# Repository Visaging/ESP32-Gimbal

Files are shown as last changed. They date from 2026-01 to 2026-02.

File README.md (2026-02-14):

# Over-Engineered Stick (ESP32-S3 Gimbal)
Because apparently holding a phone parallel to the ground requires too much caloric burn for the modern human, I spent some time engineering a robot to do it for me. This is a custom 3-axis gimbal powered by an ESP32-S3, designed to compensate for your lack of wrist stability and general unwillingness to hold a steady shot.

## The "Why Did I Build This" Stack:
- **MCU:** ESP32-S3-WROOM-1-N8R2 _(Because a simple Arduino wasn't overkill enough)_
- **Sensors:** BMI270 6-Axis IMU _(To feel every single one of your hand tremors)_
- **Drivers:** 3x DRV8313 Three-Phase Drivers _(So the phone floats magically while you do nothing)_
- **Motors:** 2805 140KV Gimbal BLDC Motors _(To turn in exactly the opposite direction like she did)_
- **Power:** Custom 3S Li-Ion BMS with CN3303 Charging & TPS563200 Regulation _(Because USB 5V is for the weak)_

## Key Features
- **Active Stabilization:** Uses high-frequency FOC math to micro-manage gravity so you don't have to use "muscles".
- **Native USB-C:** One cable to code it and charge it, because looking for two different cables is just too much work.
- **3 Operation Modes:**
   * Stabilize: Standard horizon leveling and pan following.
   * Teaching Mode: Disables the motors so you can twist the camera to any weird angle by hand. After 5 seconds of holding it there, the gimbal accepts its new reality and locks that position.
   * Selfie/Statue Mode: A dedicated mode that gives you 6 seconds to pose the camera, then freezes it in place indefinitely because apparently holding a selfie angle is considered cardio now.
<hr></hr>
<details>
  <summary><h2>External Wiring Diagrams</h2></summary>
  
### Battery:

<!--
https://mermaid.live/edit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
-->
<hr></hr>

### Handle wiring:

<!--
https://mermaid.live/edit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
-->
<hr></hr>

### BMI270 Breakout Board:

<!--
https://mermaid.live/edit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
-->
<hr></hr>

### Motors:

<!--
https://mermaid.live/edit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
-->

</details>
<hr></hr>
<details>
  <summary><h2>PCB Schematics</h2></summary>


</details>
<hr></hr>
<details>
  <summary><h2>PCB Layout and Render</h2></summary>


</details>
<hr></hr>
<details>
  <summary><h2>Custom Body (3D Model)</h2></summary>

### Handle:


<hr></hr>

### Handle Top:


<hr></hr>

### Handle Enclosure:


<hr></hr>

### PAN Arm :


<hr></hr>

### ROLL Arm:


<hr></hr>

### PITCH Arm:


<hr></hr>

### PITCH Arm Cover:


<hr></hr>

### Tripod Enclosure:


<hr></hr>

### Tripod Hub:


<hr></hr>

### Tripod Legs:


</details>
<hr></hr>

## Financial Damage Report (Bill of Material)
BOM can be found in the  root older as a .csv, and is also viewable here: [Custom Gimble BOM](https://docs.google.com/spreadsheets/d/1aBBvSRlrgi5838ZnFZRnFuO4f2IFtYvHOy1n1r-4Mq0/edit?usp=sharing)
<details>
  <summary>Lion Circuits Order Order</summary>
  



</details>
<details>
  <summary>Carts</summary>
  
### Robu
  
Robu
<hr></hr>

### OnlyScrews

OnlyScrews
<hr></hr>

### ElectroPi

ElectroPi
<hr></hr>

### Evalta

Evalta
<hr></hr>

### DNA Tech India


<hr></hr>

### Amazon
Amazon
</details>

## Future Bugs... I Mean Features (Roadmap)
Things I might add if I ever get bored of it working perfectly

- [ ] Bluetooth App: Control the gimbal with a phone _(because looking at two screens is better than one)._
- [ ] Face Tracking: If I can figure out how to run AI on this chip without it catching fire.

## Liability Waiver (License)
**License:** MIT

Feel free to steal this code, modify it, or sell it. However, if your phone falls out and breaks because you set the PID values wrong, I legally never met you.

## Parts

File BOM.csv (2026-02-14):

Item | Description | Quantity | Unit Price ($) | Total Price ($) | URL | Total ($)
PCBA | PCB | 5 PCB, 1 PCBA | 167.9 | 167.9 | https://jlcpcb.com/ | 167.9
BMI270 Breadout Board | IMU | 1 | 3.46 | 3.46 | https://evelta.com/7semi-bmi270-nano-6-axis-imu-sensor-board-qwiic/ | 171.36
2805 140KV BLDC Motors | Motors | 3 | 11.88 | 35.64 | https://www.electropi.in/2805-140kv-gimbal-brushless-motor | 207
3.6v 2600mah 18650 Li-Ion Battery | Battery | 3 | 2.4 | 7.2 | https://robu.in/product/bak-nmc-18650-2600mah-3c-lithium-ion-3-6v-battery/ | 214.2
18650 3×1 Cell Spacer | Cell Spacer | 2 | 0.011 | 0.022 | https://robu.in/product/18650-3x1-battery-cell-spacer-holder/ | 214.222
3S 10A Li-ion 18650 BMS | BMS | 1 | 1.48 | 1.48 | https://robu.in/product/3s-6a-li-ion-18650-charger-protection-board-module-10-8v-11-1v-12-6v/ | 215.702
DS-316 10MM Momentary Push Button | Push Buttons | 3 | 0.25 | 0.75 | https://robu.in/product/red-ds-316-10mm-lock-free-momentary-self-reset-small-push-button-switch/ | 216.452
3A 250V Rocker Swtich | Power Botton | 1 | 0.27 | 0.27 | https://robu.in/product/1-month-warranty-1217/ | 216.722
3mm LED Orange | LED | 8 | 0.014 | 0.112 | https://robu.in/product/3mm-dip-led-orange-50-pcs/ | 216.834
30AWG Silicon Wire (Red) | Connecting Wire | 5 | 0.055 | 0.275 | https://robu.in/product/high-quality-ultra-flexible-30awg-silicone-wire-1000-m-red/ | 217.109
30AWG Silicon Wire (Black) | Connecting Wire | 5 | 0.055 | 0.275 | https://robu.in/product/high-quality-ultra-flexible-30awg-silicone-wire-1000-m-black/ | 217.384
30AWG Silicon Wire (Yellow) | Connecting Wire | 5 | 0.055 | 0.275 | https://robu.in/product/high-quality-ultra-flexible-30awg-silicone-wire-yellow/ | 217.659
30AWG Silicon Wire (Green) | Connecting Wire | 5 | 0.055 | 0.275 | https://robu.in/product/high-quality-ultra-flexible-30awg-silicone-wire-green/ | 217.934
CN3303 | Booster Chip | 1 | 0.55 | 0.55 | https://www.dnatechindia.com/cn3303-pfm-three-cell-lithium-battery-ic.html | 218.484
TYPE-C-31-M-12 | USB-C Port | 1 | 0.42 | 0.42 | https://robu.in/product/type-c-31-m-12-hroparts-5a-1-16p-female-type-c-smd-usb-connectors-rohs/?gad_source=1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 | 218.904
Universal Mobile Holder | Mobile Holder | 1 | 1.54 | 1.54 | https://www.amazon.in/gp/product/B07S9KNGVS | 220.444
M2 and M3 Screws | Mounting Screws | 1 | 4.41 | 4.41 | https://www.amazon.in/gp/product/B0FP53QGD2/ | 224.854
3M VHB Tape | Mounting PCB | 1 | 1.22 | 1.22 | https://onlyscrews.in/products/3m%E2%84%A2-foam-tape-12mm-x-5meters | 226.074
M3 x 10mm Screws | Mounting Screws | 4 | 0.015 | 0.06 | https://onlyscrews.in/products/phillips-csk-m3-x-8mm-pack-of-20? | 226.134
M3 x 8mm Inserts | Mounting Inserts | 4 | 0.029 | 0.116 | https://onlyscrews.in/products/m3-x-8mm-brass-threaded-inserts? | 226.25
M3 x 25mm Screws | Mounting Screws | 3 | 0.026 | 0.078 | https://onlyscrews.in/products/m3-x-25mm-phillips-csk-ss-304-screw? | 226.328
M3 Nylock Nuts | Mounting Nuts | 3 | 0.033 | 0.099 | https://onlyscrews.in/products/m3-nyloc-nuts-ss304? | 226.427
1/4" - 20 D-Ring | Tripod/Clamp Mounting screw | 1 | 4.42 | 4.42 | https://www.amazon.in/SHOPEE-Mounting-Adapter-Camcorder-Stainless/dp/B09S3XQ8R9/ | 230.847
Platform | Total Shipping + Tax ($) | Running Total ($)
Lion Circuits | 0 | 230.847
Amazon | 0 | 230.847
Robu | 0 | 230.847
Evalta | 0.5 | 231.347
Electropi | 0 | 231.347
DNA Tech India | 1.13 | 232.477
Only Screws | 1.83 | 234.307
Price Buffer | 2 | 236.307
Printing Legion (3D Printing) | 15 | 251.307

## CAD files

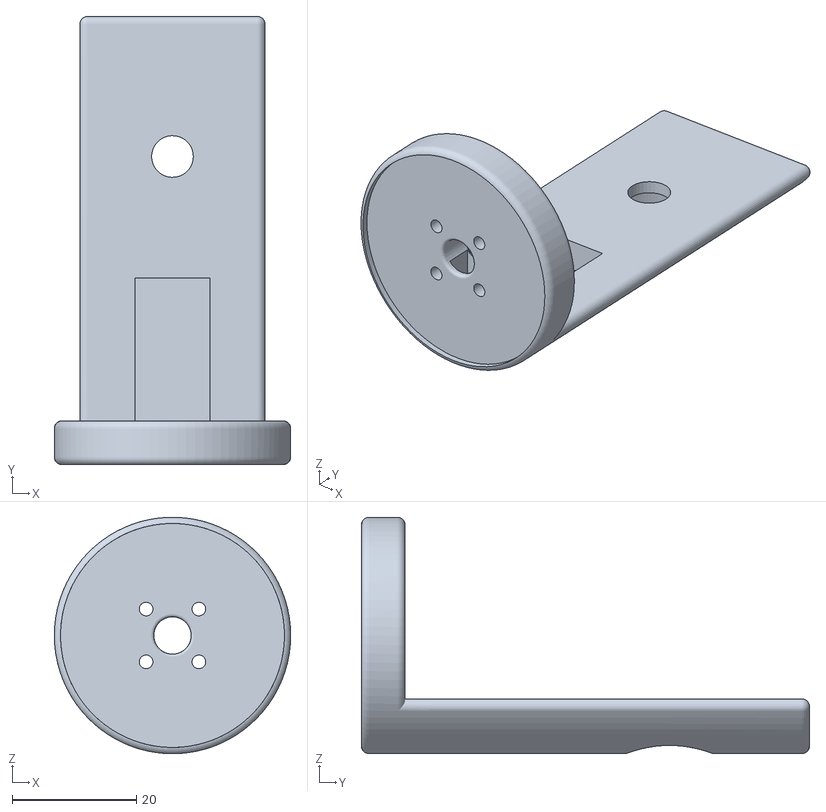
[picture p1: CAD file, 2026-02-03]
CAD/PITCH-Arm.stl
38.0 x 72.0 x 38.0

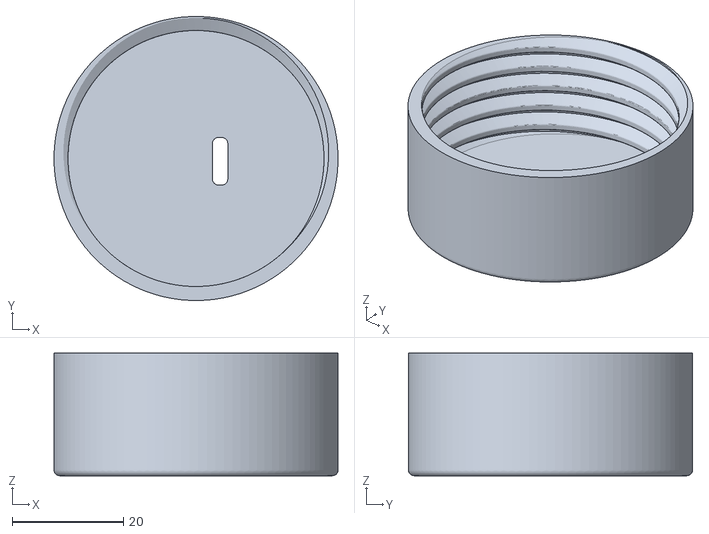
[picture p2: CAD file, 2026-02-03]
CAD/Handle-Enclosure.stl
51.0 x 51.0 x 22.0

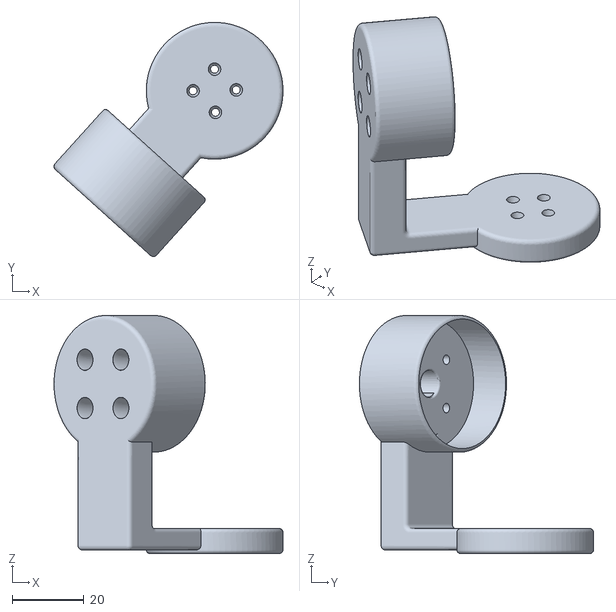
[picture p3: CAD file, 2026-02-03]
CAD/PAN-Arm V2.stl
63.6 x 65.1 x 66.2

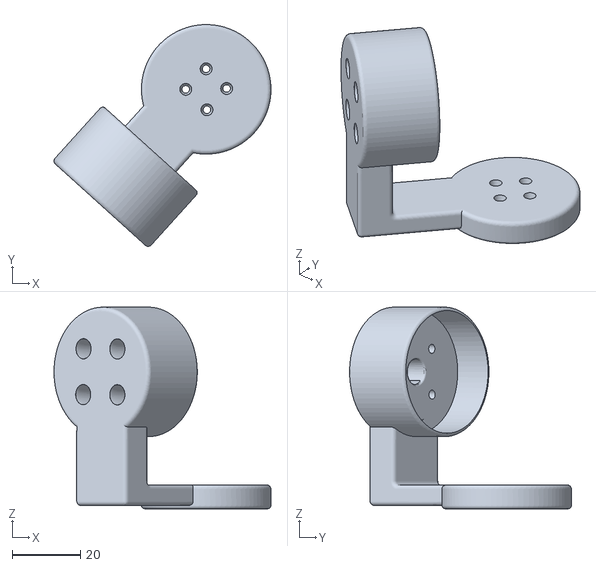
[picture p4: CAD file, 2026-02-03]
CAD/ROLL-Arm V2.stl
63.6 x 65.1 x 59.1

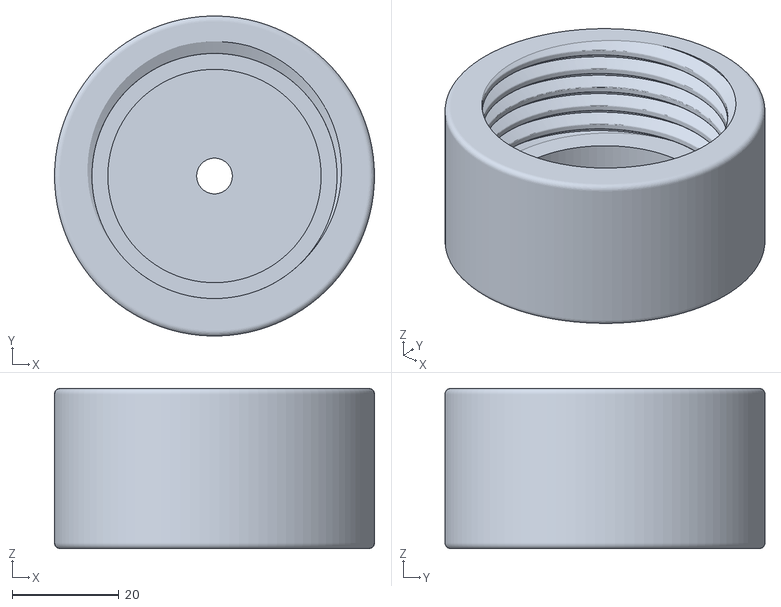
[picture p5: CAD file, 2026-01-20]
CAD/Tripod-Enclosure.stl
60.0 x 60.0 x 30.0

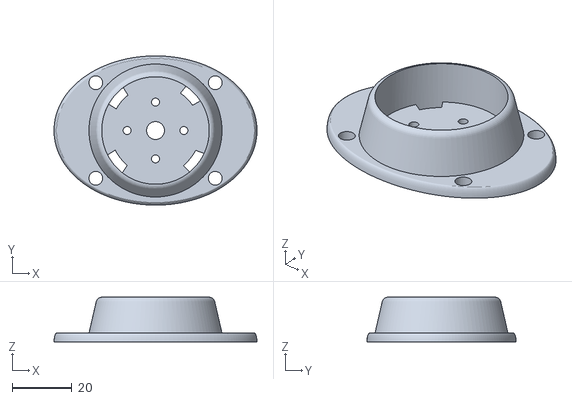
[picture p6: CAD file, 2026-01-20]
CAD/Handle-Top.stl
68.0 x 50.0 x 15.0

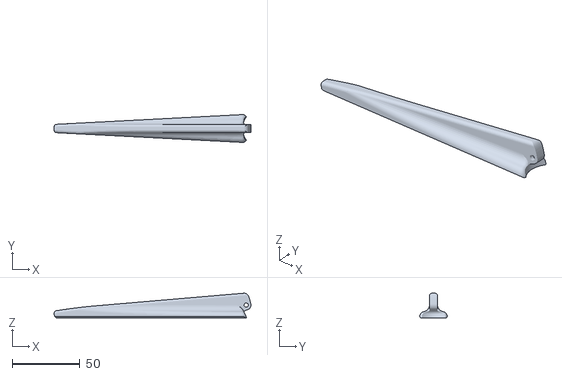
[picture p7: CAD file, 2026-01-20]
CAD/Tripod-Leg.stl
145.5 x 20.6 x 18.2

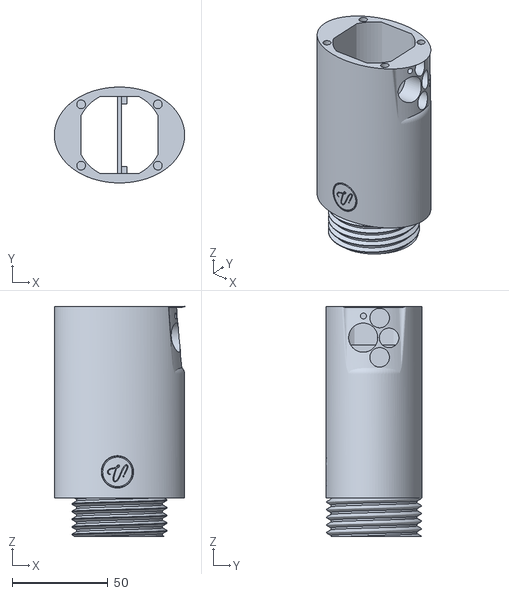
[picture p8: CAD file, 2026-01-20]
CAD/Handle.stl
68.0 x 50.0 x 120.0

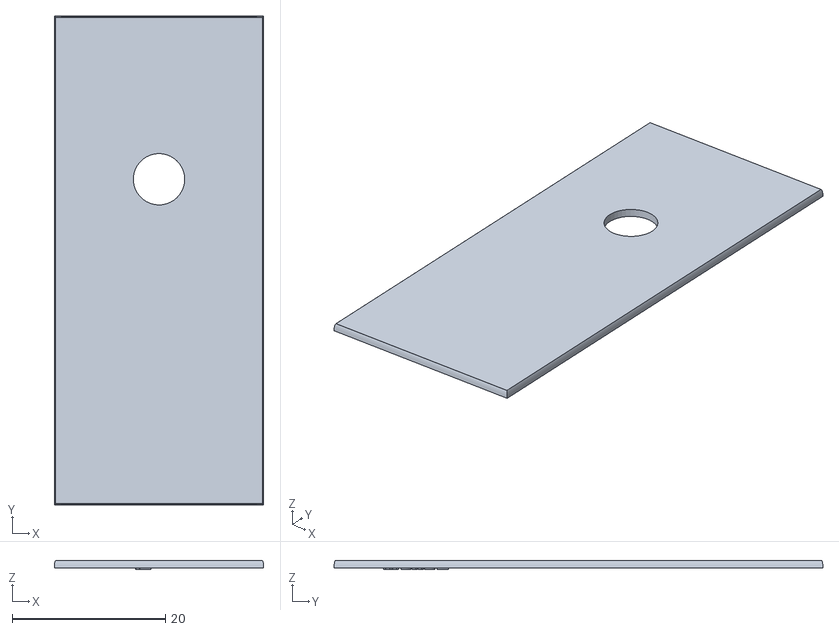
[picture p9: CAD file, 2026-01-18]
CAD/Pitch-Arm-Cover.stl
27.3 x 63.8 x 1.20

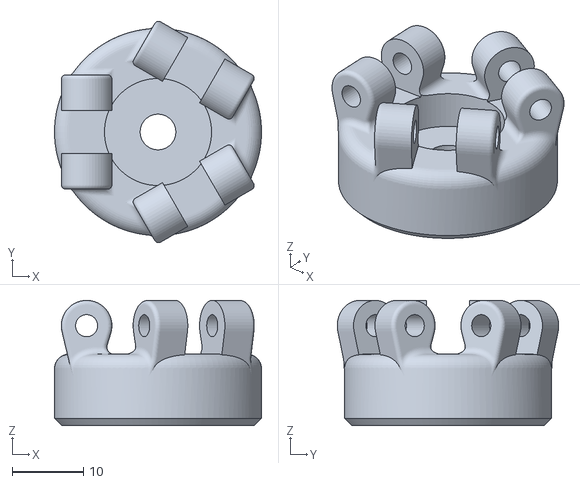
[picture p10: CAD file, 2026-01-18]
CAD/Tripod-Hub.stl
29.0 x 31.0 x 17.5

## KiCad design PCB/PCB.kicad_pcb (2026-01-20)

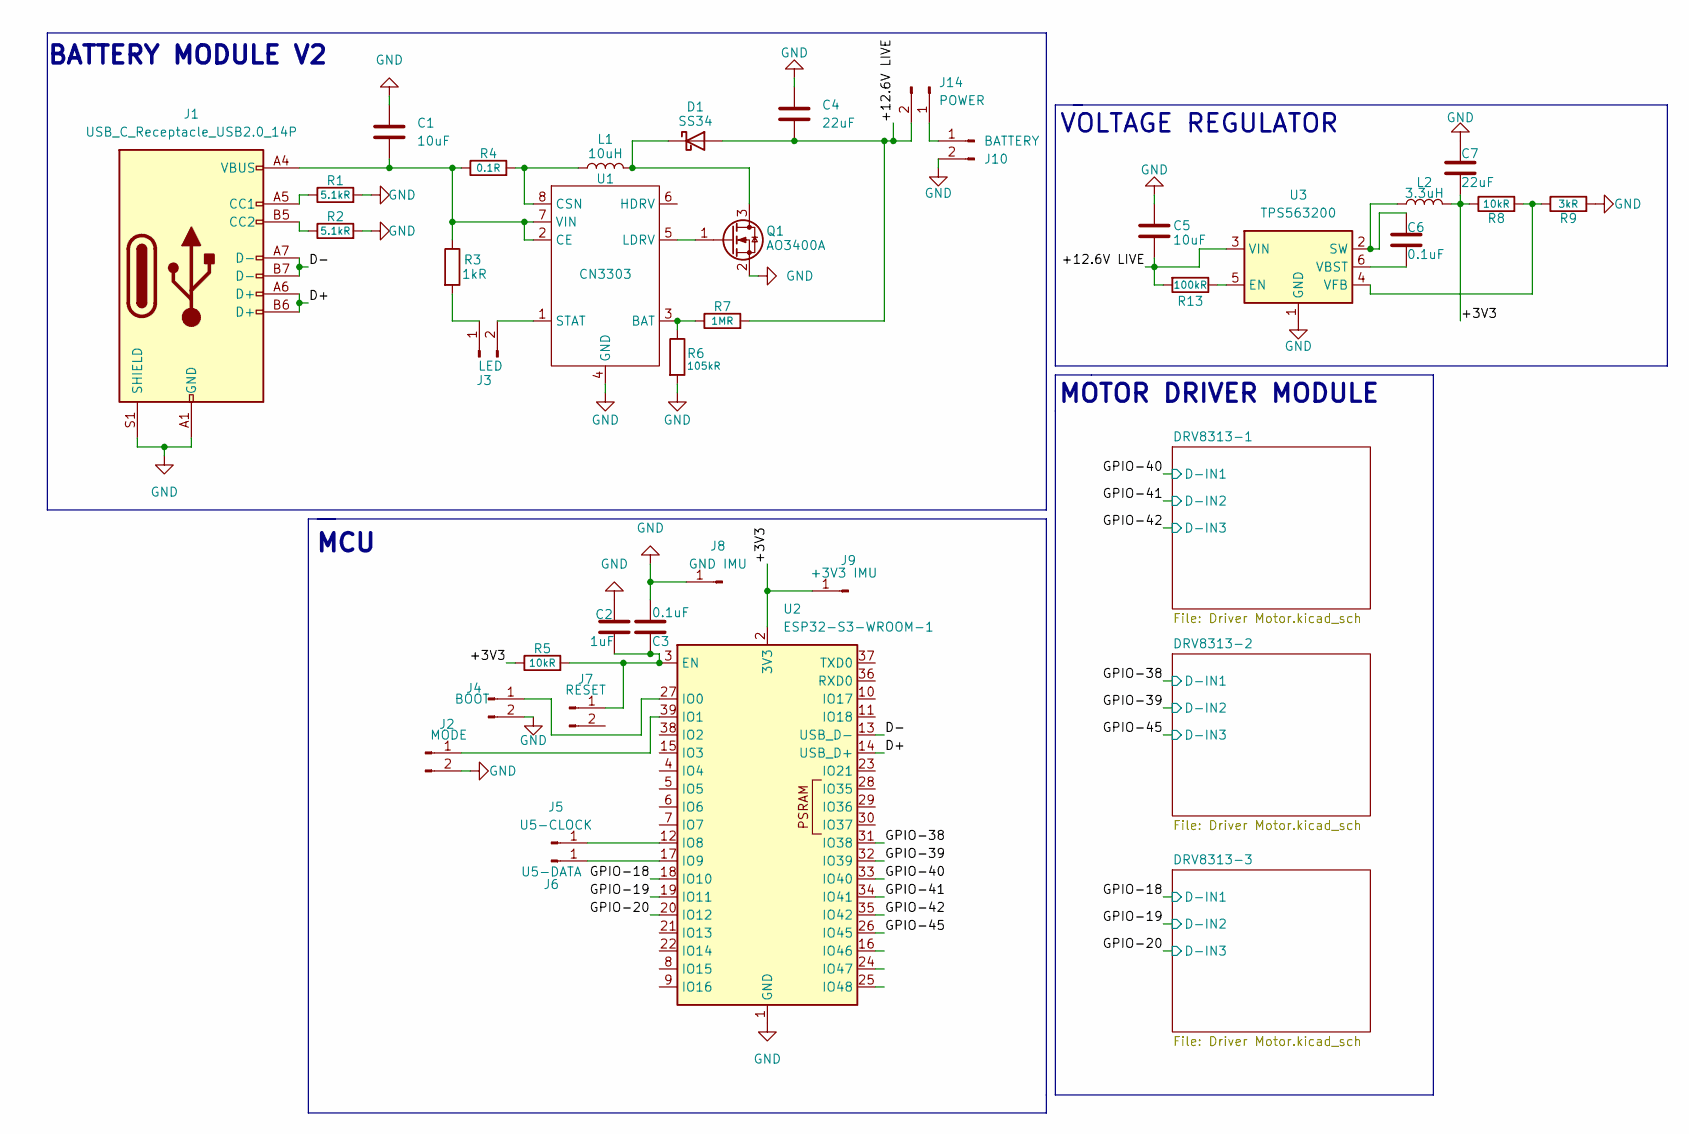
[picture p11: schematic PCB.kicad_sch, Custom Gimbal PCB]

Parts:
C1, C5: 10uF; C_0805_2012Metric
C2: 1uF; C_0805_2012Metric
C3, C6: 0.1uF; C_0805_2012Metric
C4, C7: 22uF; C_0805_2012Metric
D1: SS34; D_SMA
J1: USB_C_Receptacle_USB2.0_14P; USB_C_Receptacle_HRO_TYPE-C-31-M-12
J2: MODE; SolderWire-0.1sqmm_1x02_P3.6mm_D0.4mm_OD1mm
J3: LED; SolderWire-0.1sqmm_1x02_P3.6mm_D0.4mm_OD1mm
J4: BOOT; SolderWire-0.1sqmm_1x02_P3.6mm_D0.4mm_OD1mm
J5: U5-CLOCK; SolderWire-0.1sqmm_1x01_D0.4mm_OD1mm
J6: U5-DATA; SolderWire-0.1sqmm_1x01_D0.4mm_OD1mm
J7: RESET; SolderWire-0.1sqmm_1x02_P3.6mm_D0.4mm_OD1mm
J8: GND IMU; SolderWire-0.1sqmm_1x01_D0.4mm_OD1mm
J9: +3V3 IMU; SolderWire-0.1sqmm_1x01_D0.4mm_OD1mm
J10: BATTERY; SolderWire-0.1sqmm_1x02_P3.6mm_D0.4mm_OD1mm
J14: POWER; SolderWire-0.1sqmm_1x02_P3.6mm_D0.4mm_OD1mm
L1: 10uH; L_Bourns-SRN6028
L2: 3.3uH; L_1210_3225Metric
Q1: AO3400A; SOT-23
R1, R2: 5.1kR; R_0805_2012Metric_Pad1.20x1.40mm_HandSolder
R3: 1kR; R_0805_2012Metric
R4: 0.1R; R_1206_3216Metric
R5, R8: 10kR; R_0805_2012Metric
R6: 105kR; R_0805_2012Metric
R7: 1MR; R_0805_2012Metric
R9: 3kR; R_0805_2012Metric
R13: 100kR; R_0805_2012Metric
U1: CN3303; SOIC-8_3.9x4.9mm_P1.27mm
U2: ESP32-S3-WROOM-1
U3: TPS563200; SOT-23-6

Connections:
/+3V3: C7.1, J9.1, L2.2, R5.1, R8.1, U2.2 (3V3)
/+12.6V LIVE: C4.1, C5.2, D1.2 (A), J14.2, R7.2, R13.2, U3.3 (VIN)
/D+: J1.A6 (D+), J1.B6 (D+), U2.14 (USB_D+)
/D-: J1.A7 (D-), J1.B7 (D-), U2.13 (USB_D-)
/GPIO-18: U2.18 (IO10); also elsewhere on the board
/GPIO-19: U2.19 (IO11); also elsewhere on the board
/GPIO-20: U2.20 (IO12); also elsewhere on the board
/GPIO-38: U2.31 (IO38); also elsewhere on the board
/GPIO-39: U2.32 (IO39); also elsewhere on the board
/GPIO-40: U2.33 (IO40); also elsewhere on the board
/GPIO-41: U2.34 (IO41); also elsewhere on the board
/GPIO-42: U2.35 (IO42); also elsewhere on the board
/GPIO-45: U2.26 (IO45); also elsewhere on the board
GND: C1.1, C2.2, C3.2, C4.2, C5.1, C7.2, J1.A1 (GND), J1.A12 (GND), J1.B1 (GND), J1.B12 (GND), J1.S1 (SHIELD), J2.2, J4.2, J8.1, J10.2, Q1.2 (S), R1.2, R2.2, R6.2, R9.2, U1.4 (GND), U2.1 (GND), U2.40 (GND), U2.41 (GND), U3.1 (GND); also elsewhere on the board
unnamed: D1.1 (K), L1.2, Q1.3 (D)
unnamed: J1.A5 (CC1), R1.1
unnamed: J1.B5 (CC2), R2.1
unnamed: J2.1, U2.39 (IO1)
unnamed: J3.1, R3.2
unnamed: J3.2, U1.1 (STAT)
unnamed: J4.1, U2.27 (IO0)
unnamed: J5.1, U2.12 (IO8)
unnamed: J6.1, U2.17 (IO9)
unnamed: C2.1, C3.1, J7.1, R5.2, U2.3 (EN)
unnamed: J10.1, J14.1
unnamed: Q1.1 (G), U1.5 (LDRV)
unnamed: R6.1, R7.1, U1.3 (BAT)
unnamed: C1.2, J1.A4 (VBUS), J1.A9 (VBUS), J1.B4 (VBUS), J1.B9 (VBUS), R3.1, R4.1, U1.2 (CE), U1.7 (VIN)
unnamed: L1.1, R4.2, U1.8 (CSN)
unnamed: R13.1, U3.5 (EN)
unnamed: C6.1, L2.1, U3.2 (SW)
unnamed: C6.2, U3.6 (VBST)
unnamed: R8.2, R9.1, U3.4 (VFB)

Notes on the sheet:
MOTOR DRIVER MODULE
BATTERY MODULE V2
MCU
VOLTAGE REGULATOR

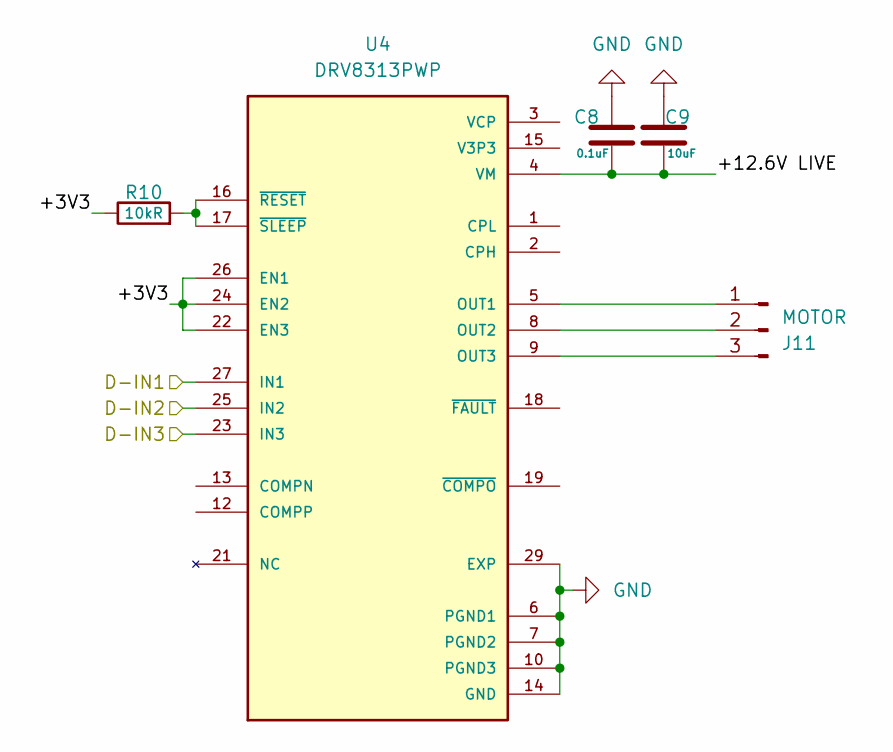
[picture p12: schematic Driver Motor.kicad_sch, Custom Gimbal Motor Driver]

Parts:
C8: 0.1uF; C_0805_2012Metric
C9: 10uF; C_0805_2012Metric
J11: MOTOR; SolderWire-0.1sqmm_1x03_P3.6mm_D0.4mm_OD1mm
R10: 10kR; R_0805_2012Metric
U4: DRV8313PWP; SOP65P640X120-29N; PARTREV D

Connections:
/DRV8313-1/+3V3: R10.1, U4.22 (EN3), U4.24 (EN2), U4.26 (EN1)
/GPIO-40: U4.27 (IN1); also elsewhere on the board
/GPIO-41: U4.25 (IN2); also elsewhere on the board
/GPIO-42: U4.23 (IN3); also elsewhere on the board
GND: C8.2, C9.1, U4.6 (PGND1), U4.7 (PGND2), U4.10 (PGND3), U4.14 (GND), U4.20 (GND), U4.28 (GND), U4.29 (EXP); also elsewhere on the board
unnamed: J11.1, U4.5 (OUT1)
unnamed: J11.2, U4.8 (OUT2)
unnamed: J11.3, U4.9 (OUT3)
unnamed: R10.2, U4.16 (~RESET), U4.17 (~SLEEP)
VM: C8.1, C9.2, U4.4 (VM), U4.11 (VM); also elsewhere on the board

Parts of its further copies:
C10, C12: 0.1uF; C_0805_2012Metric
C11, C13: 10uF; C_0805_2012Metric
J12, J13: MOTOR; SolderWire-0.1sqmm_1x03_P3.6mm_D0.4mm_OD1mm
R11, R12: 10kR; R_0805_2012Metric
U5, U6: DRV8313PWP; SOP65P640X120-29N; PARTREV D

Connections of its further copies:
/DRV8313-2/+3V3: R11.1, U5.22 (EN3), U5.24 (EN2), U5.26 (EN1)
/DRV8313-3/+3V3: R12.1, U6.22 (EN3), U6.24 (EN2), U6.26 (EN1)
/GPIO-18: U6.27 (IN1); also elsewhere on the board
/GPIO-19: U6.25 (IN2); also elsewhere on the board
/GPIO-20: U6.23 (IN3); also elsewhere on the board
/GPIO-38: U5.27 (IN1); also elsewhere on the board
/GPIO-39: U5.25 (IN2); also elsewhere on the board
/GPIO-45: U5.23 (IN3); also elsewhere on the board
GND: C10.2, C11.1, C12.2, C13.1, U5.6 (PGND1), U5.7 (PGND2), U5.10 (PGND3), U5.14 (GND), U5.20 (GND), U5.28 (GND), U5.29 (EXP), U6.6 (PGND1), U6.7 (PGND2), U6.10 (PGND3), U6.14 (GND), U6.20 (GND), U6.28 (GND), U6.29 (EXP); also elsewhere on the board
unnamed: J12.1, U5.5 (OUT1)
unnamed: J12.2, U5.8 (OUT2)
unnamed: J12.3, U5.9 (OUT3)
unnamed: J13.1, U6.5 (OUT1)
unnamed: J13.2, U6.8 (OUT2)
unnamed: J13.3, U6.9 (OUT3)
unnamed: R11.2, U5.16 (~RESET), U5.17 (~SLEEP)
unnamed: R12.2, U6.16 (~RESET), U6.17 (~SLEEP)
VM: C10.1, C11.2, C12.1, C13.2, U5.4 (VM), U5.11 (VM), U6.4 (VM), U6.11 (VM); also elsewhere on the board

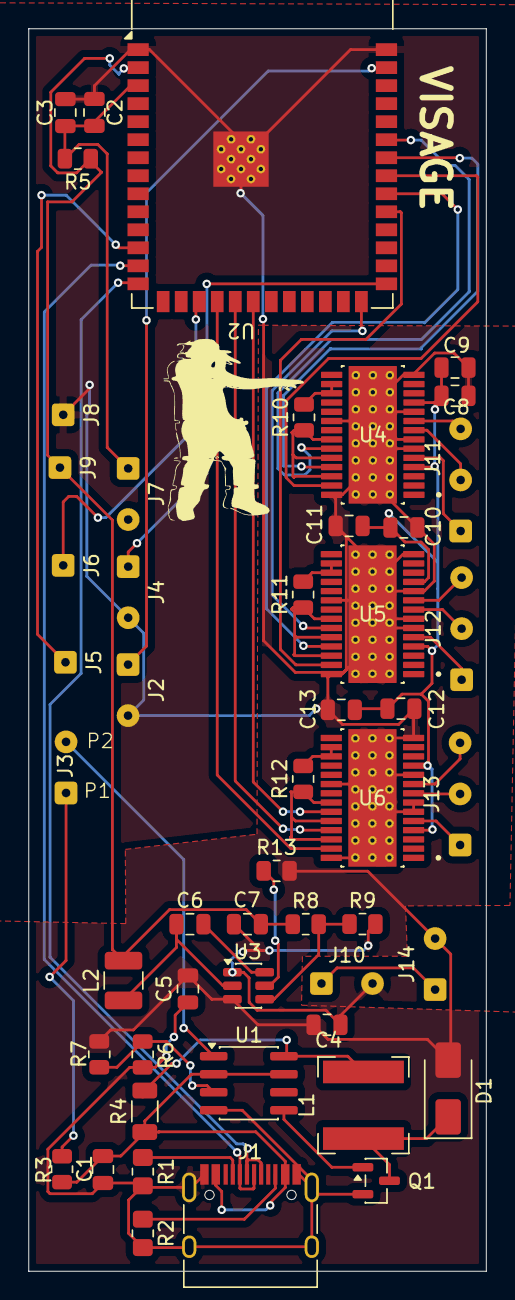
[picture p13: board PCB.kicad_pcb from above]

Board: 2 copper layers, 32.2 x 87.6 mm, 50 parts (0 on the bottom side), 49 nets.
